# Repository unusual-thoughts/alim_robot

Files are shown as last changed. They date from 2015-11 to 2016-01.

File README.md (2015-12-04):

Réalisation de la carte d'alimentation
======================================

La carte d'alimentation est chargée de:
- Délivrer l'alimentation des différents composants du robot
- Informer de l'état de charge des batteries avec des leds
- Protéger les batteries

### Ancienne Carte

Un microcontrôleur Atmega328P utilisé pour évaluer la tension des batteries.

Les sources étaient trois batteries NiMh 12V de 2500mAh

Les régulateurs utilisés étaient DE-5W050 et DE-5WADJ

On peut utiliser des LM2596 a la place
Le plus simple serait de prendre des modules déja faits (très très peu chers)

### Budget Courant/tension

Elément            | U (V) | I (mA)             | P (W)
-------------------|-------|--------------------|------
Autres capteurs    | 3,3   | 5-50               | < .3
Raspberry          | 5     | 700 (1.5A max)     | < 7.5
Arduino/Teensy     | 5     | 10-20 (optimiste?) | ~.1
Capteurs           | 5     | 5-50               | < .5
Hokuyo             | 5     | 500 (800 init)     | < 4
Pont en H          | 5     | 5-10               | < .05
uArm               | 5     | < 5A               | < 25
Total 5V           | 5     | ~7A                | ~35
Servo Dynamixel    | 11.1  | 1.3A (x2)          | 28.86
Moteurs            | 24    | 800 (pic)          | < 38.4
Total (bat 1 et 2) | 24    | < 800              | < 38.4
Total (bat 3)      | 12    | < 5.42 A           | < 65

### Choix Régulateur(s)

Dynamixels non régulés? Ou step-down depuis le 24V? ou 12V?

Utilisation de [WEBENCH](http://webench.ti.com/) pour choix régulateur.

Régulateur                                            | Courant  | Package | Commentaires
------------------------------------------------------|----------|---------|----------------------------------------------
[Module LM2596](http://www.ebay.com/itm/321476590827) | << 3A    | Module  | Peu fiable (!)
[LM2596](http://www.ti.com/product/lm2596)            | max 3A   | ~TO263  | Pas assez de courant
[LM2678](http://www.ti.com/product/lm2678)            | max 5A   | ~TO263  | Fort encombrement, courant insuffisant, gros inducteur et diode
[TPS54821](http://www.ti.com/product/tps54821)        | max 8A   | QFN     | très performant, pas cher, très faible encombrement, compliqué à souder
[LMZ12008](http://www.ti.com/product/LMZ12008/)       | max 8A   | PFM     | très encombrant, très simple d'utilisation, extremement cher (15 euros)
[LMZ31710](http://www.ti.com/product/LMZ31710)        | max 10A  | QFN     | compromis, peu de composants externes, pas d'inducteur (!)

### Choix batterie 12V

On garde les 2 NiMh pour le 24V
LiPo pour le 12V:
[5800mAh](http://www.hobbyking.com/hobbyking/store/uh_viewItem.asp?idProduct=35957) ou [8000mAh](http://www.hobbyking.com/hobbyking/store/__38300__ZIPPY_Flightmax_8000mAh_3S1P_30C_Lipo_Pack_EU_Warehouse_.html)

### Schematic
#### Cicuit de protection batterie


#### Arduino


### Aperçu carte


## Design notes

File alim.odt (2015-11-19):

Réalisation de la carte d'alimentation

La carte d'alimentation est chargée :

-délivrer l'alimentation des différents composants du robot

-informer de l'état de charge des batteries avec des leds

Un microcontroleur Atmega328P sera utilisé pour évalué la tenion des batteries.

Les sources sont trois batteries 12V de 2500mAh

Les régulateurs utilisés sont DE-5W050 et DE-5WADJ

Entrés | Régulateur Dimension Engineering | Sortie
7-30V | | 5V 1A(max)

Elément | U (V) | I (mA) | Reg
Raspberry | 5 | 700
Arduino/Teensy | 5 | 10-20
Capteurs | 5 | 5-50
Autres capteurs | 3,3 | 5-50
Hokuyo | 5 | 500 (800 init)
Pont en H | 5 | 5-10
Servomoteurs (6) | 5-8 | 400 (800 max)
Autres actionneurs
Moteurs | 24 | ?

Démarche:

- Stratégie d'alimentation

- Représentation du schématics sous Eagle

- Agencement et réalisation de la carte

- Choix de la connectique

- Choix des régulateurs

- Choix du micro, ATTiny 48/85

-Choix de batterie 18-650

Tâche :

Programmer un Atmega328P

Utilisation d'Eagle (voir tutos de Jeremy Blum)

Matériel : Régulateur 5,1 V

Etat des lieux des régulateurs présent sur les cartes :

Teensy

Arduino

Raspberry

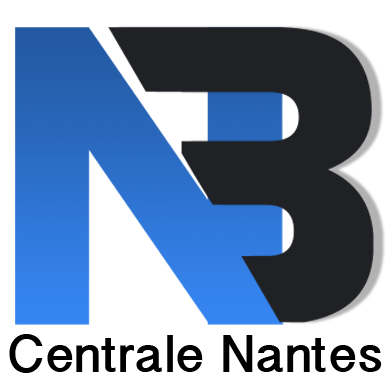
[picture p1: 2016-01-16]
eagle/artwork/Fanart.png

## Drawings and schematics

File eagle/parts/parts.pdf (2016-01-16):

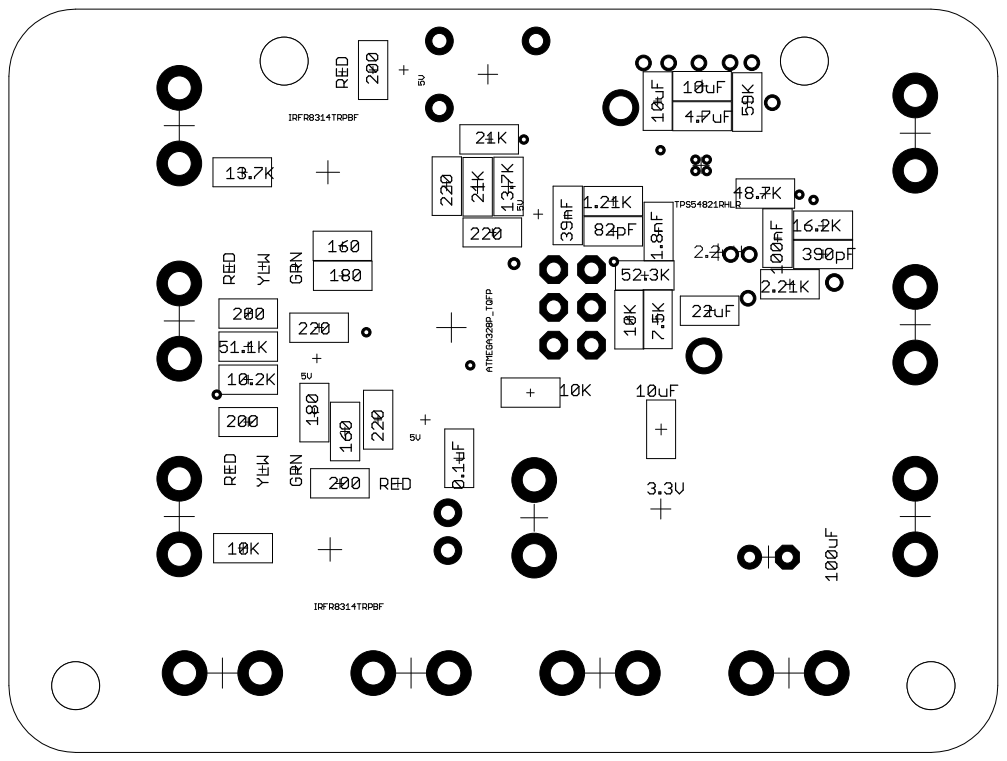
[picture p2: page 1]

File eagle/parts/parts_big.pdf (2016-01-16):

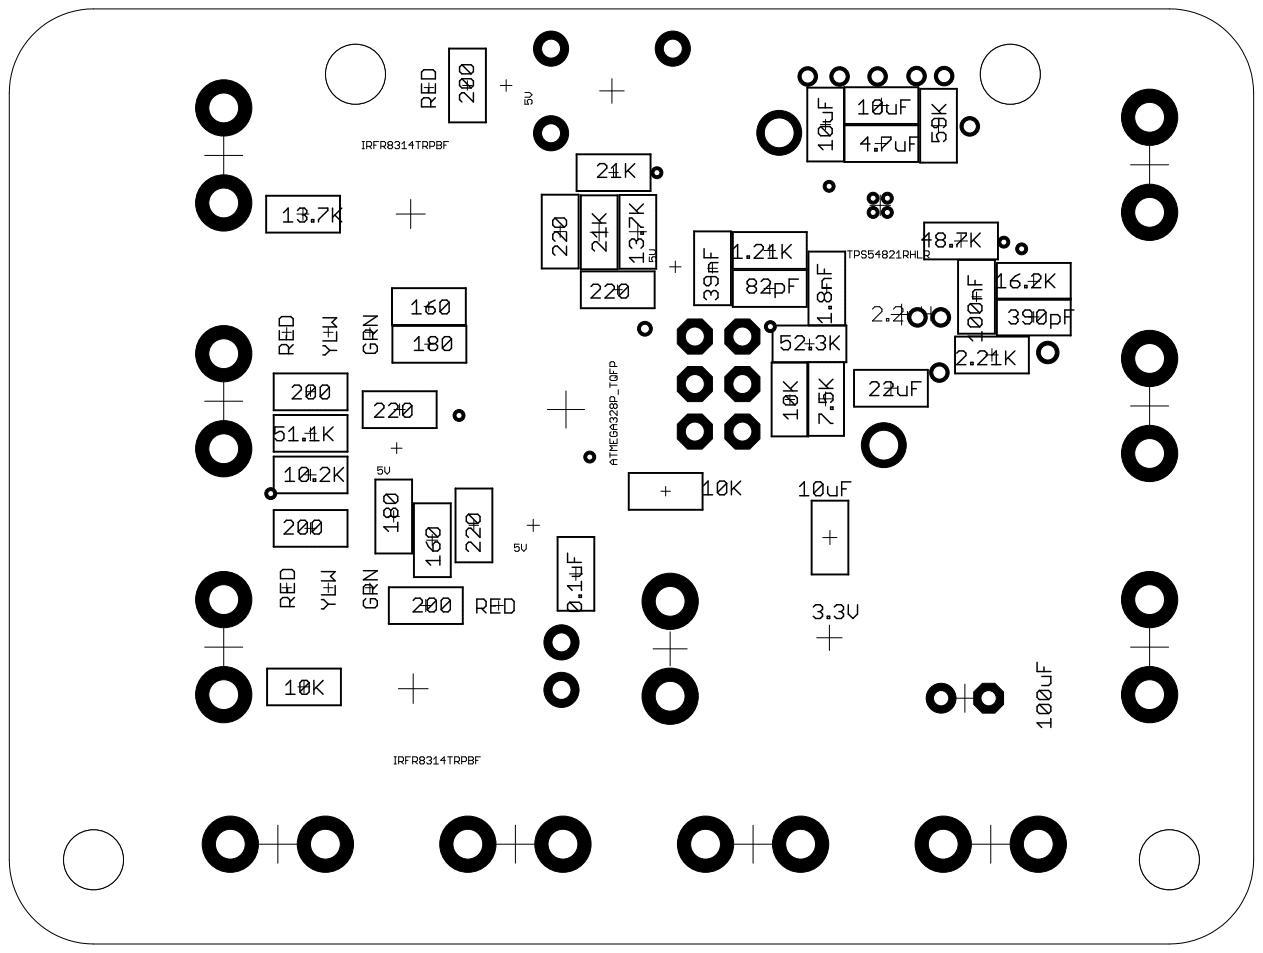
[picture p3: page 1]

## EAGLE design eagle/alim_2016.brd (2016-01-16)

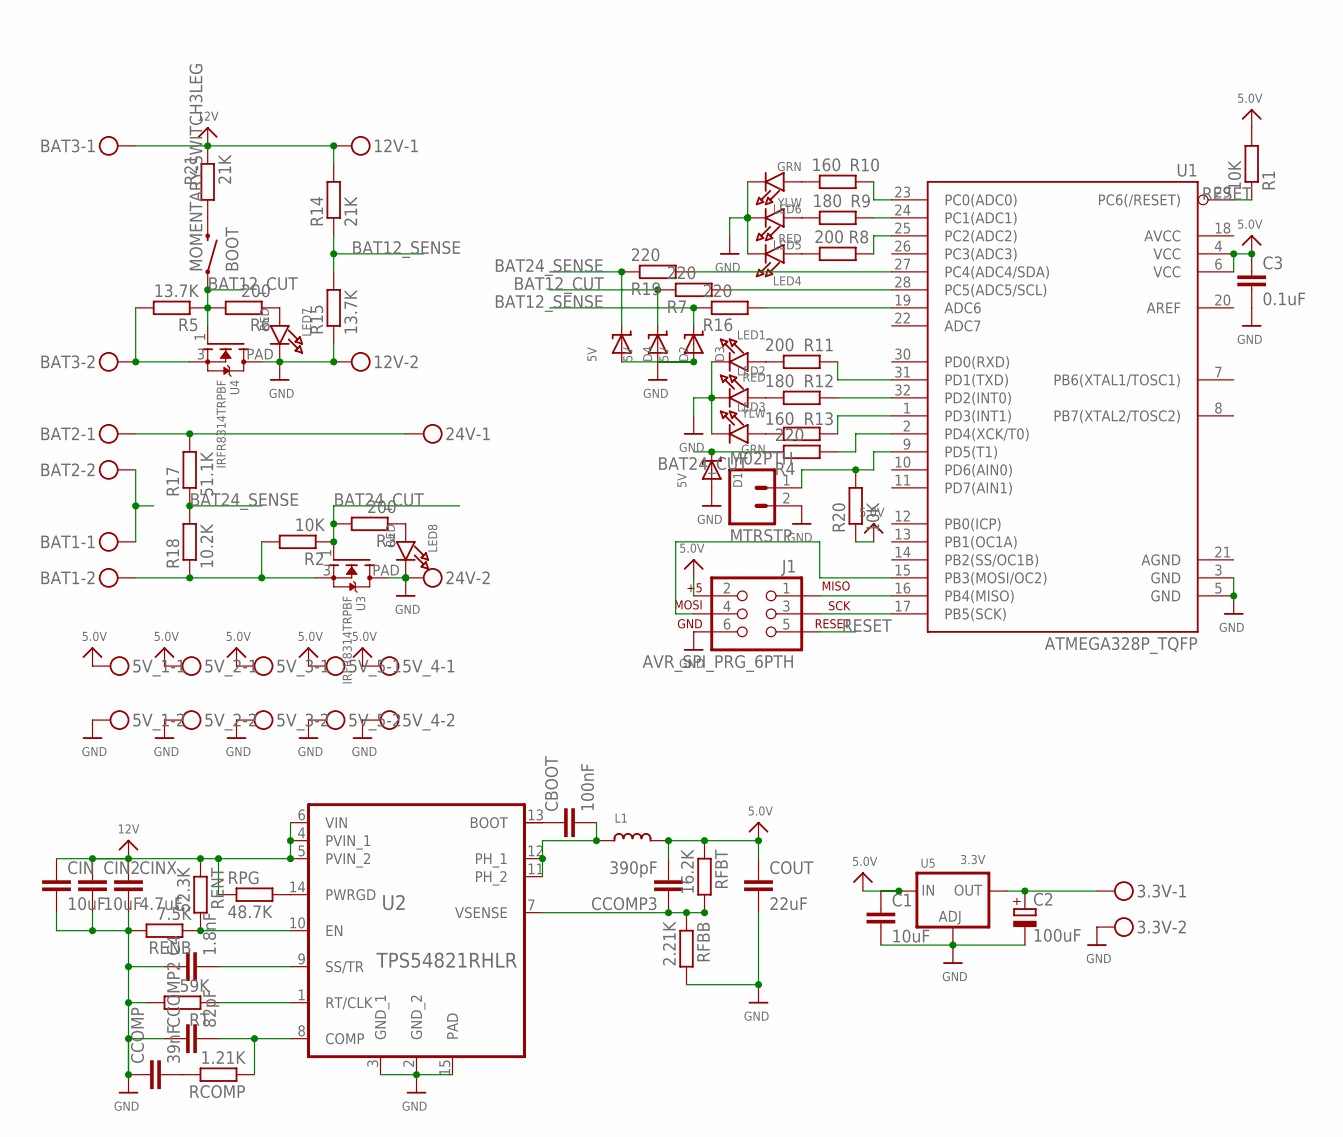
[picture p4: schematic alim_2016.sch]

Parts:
3.3V, 5V_1, 5V_2, 5V_3, 5V_4, 5V_5, 12V, 24V: WURTH_2PIN311; WURTH311
BAT1, BAT2, BAT3: WURTH_2PIN313; WURTH313_2
BOOT: MOMENTARY-SWITCH3LEG; 3LEGGED-TACT
C1: 10uF; C0805
C2: 100uF; E2,5-7
C3: 0.1uF; C0805
C4: 1.8nF; C0805
CBOOT: 100nF; C0805
CCOMP: 39nF; C0805
CCOMP2: 82pF; C0805
CCOMP3: 390pF; C0805
CIN, CIN2: 10uF; C0805
CINX: 4.7uF; C0805
COUT: 22uF; C0805
D1, D2, D3, D4: 5V; SOD-123
J1: AVR_SPI_PRG_6PTH; 2X3
L1: 2.2uH; XAL5030
LED1, LED4, LED7, LED8: RED; CHIPLED_0805_NOOUTLINE
LED2, LED5: YLW; CHIPLED_0805_NOOUTLINE
LED3, LED6: GRN; CHIPLED_0805_NOOUTLINE
MTRSTP: M02PTH; 1X02
R1, R2, R20: 10K; M0805
R3, R6, R8, R11: 200; M0805
R4, R7, R16, R19: 220; M0805
R5, R15: 13.7K; M0805
R9, R12: 180; M0805
R10, R13: 160; M0805
R14, R21: 21K; M0805
R17: 51.1K; M0805
R18: 10.2K; M0805
RCOMP: 1.21K; M0805
RENB: 7.5K; M0805
RENT: 52.3K; M0805
RFBB: 2.21K; M0805
RFBT: 16.2K; M0805
RPG: 48.7K; M0805
RT: 59K; M0805
U1: ATMEGA328P_TQFP; TQFP32-08
U2: TPS54821RHLR; S-PVQFN-N14
U3, U4: IRFR8314TRPBF; DPACK_1
U5: 3.3V; TO252

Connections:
5.0V: 5V_1.P$1, 5V_2.P$1, 5V_3.P$1, 5V_4.P$1, 5V_5.P$1, C1.1, C3.1, CCOMP3.2, COUT.1, J1.2, L1.2, R1.2, R20.1, RFBT.1, U1.4 (VCC), U1.6 (VCC), U5.2 (IN)
12V: 12V.P$1, BAT3.P$1, CIN.1, CIN2.1, CINX.1, R14.2, R21.1, RENT.1, RPG.1, U2.4 (PVIN_1), U2.5 (PVIN_2), U2.6 (VIN)
24V: 24V.P$1, BAT2.P$1, R17.2
BAT12_CUT: BOOT.1, D2.C, R5.1, R6.2, R7.1, U4.1 (G)
BAT12_SENSE: D3.C, R14.1, R15.2, R16.1
BAT24_CUT: D1.C, R2.1, R3.2, R4.1, U3.1 (G)
BAT24_SENSE: D4.C, R17.1, R18.2, R19.1
COMP: CCOMP2.2, RCOMP.1, U2.8 (COMP)
EN: RENB.1, RENT.2, U2.10 (EN)
GND: 3.3V.P$2, 5V_1.P$2, 5V_2.P$2, 5V_3.P$2, 5V_4.P$2, 5V_5.P$2, 12V.P$2, 24V.P$2, C1.2, C2.-, C3.2, C4.1, CCOMP.1, CCOMP2.1, CIN.2, CIN2.2, CINX.2, COUT.2, D1.A, D2.A, D3.A, D4.A, J1.6, LED1.C, LED2.C, LED3.C, LED4.C, LED5.C, LED6.C, LED7.C, LED8.C, MTRSTP.2, R15.1, RENB.2, RFBB.2, RT.2, U1.3 (GND), U1.5 (GND), U2.2 (GND_2), U2.3 (GND_1), U2.15 (PAD), U3.PAD (D), U4.PAD (D), U5.1 (ADJ)
MISO: J1.1, U1.16 (PB4(MISO))
MOSI: J1.4, U1.15 (PB3(MOSI/OC2))
unnamed: 3.3V.P$1, C2.+, U5.3 (OUT)
unnamed: R16.2, U1.19 (ADC6)
unnamed: BAT1.P$1, BAT2.P$2
unnamed: MTRSTP.1, R20.2, U1.9 (PD5(T1))
unnamed: BOOT.3 (2), R21.2
unnamed: BAT1.P$2, R2.2, R18.1, U3.3 (S)
unnamed: LED8.A, R3.1
unnamed: LED7.A, R6.1
unnamed: R4.2, U1.2 (PD4(XCK/T0))
unnamed: BAT3.P$2, R5.2, U4.3 (S)
unnamed: R9.2, U1.24 (PC1(ADC1))
unnamed: LED4.A, R8.1
unnamed: LED5.A, R9.1
unnamed: LED6.A, R10.1
unnamed: LED1.A, R11.1
unnamed: LED2.A, R12.1
unnamed: LED3.A, R13.1
unnamed: R8.2, U1.25 (PC2(ADC2))
unnamed: R10.2, U1.23 (PC0(ADC0))
unnamed: R7.2, U1.28 (PC5(ADC5/SCL))
unnamed: R13.2, U1.1 (PD3(INT1))
unnamed: R12.2, U1.32 (PD2(INT0))
unnamed: R11.2, U1.31 (PD1(TXD))
unnamed: R19.2, U1.27 (PC4(ADC4/SDA))
unnamed: CCOMP.2, RCOMP.2
unnamed: CBOOT.1, U2.13 (BOOT)
unnamed: RPG.2, U2.14 (PWRGD)
PH: CBOOT.2, L1.1, U2.11 (PH_2), U2.12 (PH_1)
RESET: J1.5, R1.1, U1.29 (PC6(/RESET))
RTCLK: RT.1, U2.1 (RT/CLK)
SCK: J1.3, U1.17 (PB5(SCK))
SSTR: C4.2, U2.9 (SS/TR)
VSENSE: CCOMP3.1, RFBB.1, RFBT.2, U2.7 (VSENSE)

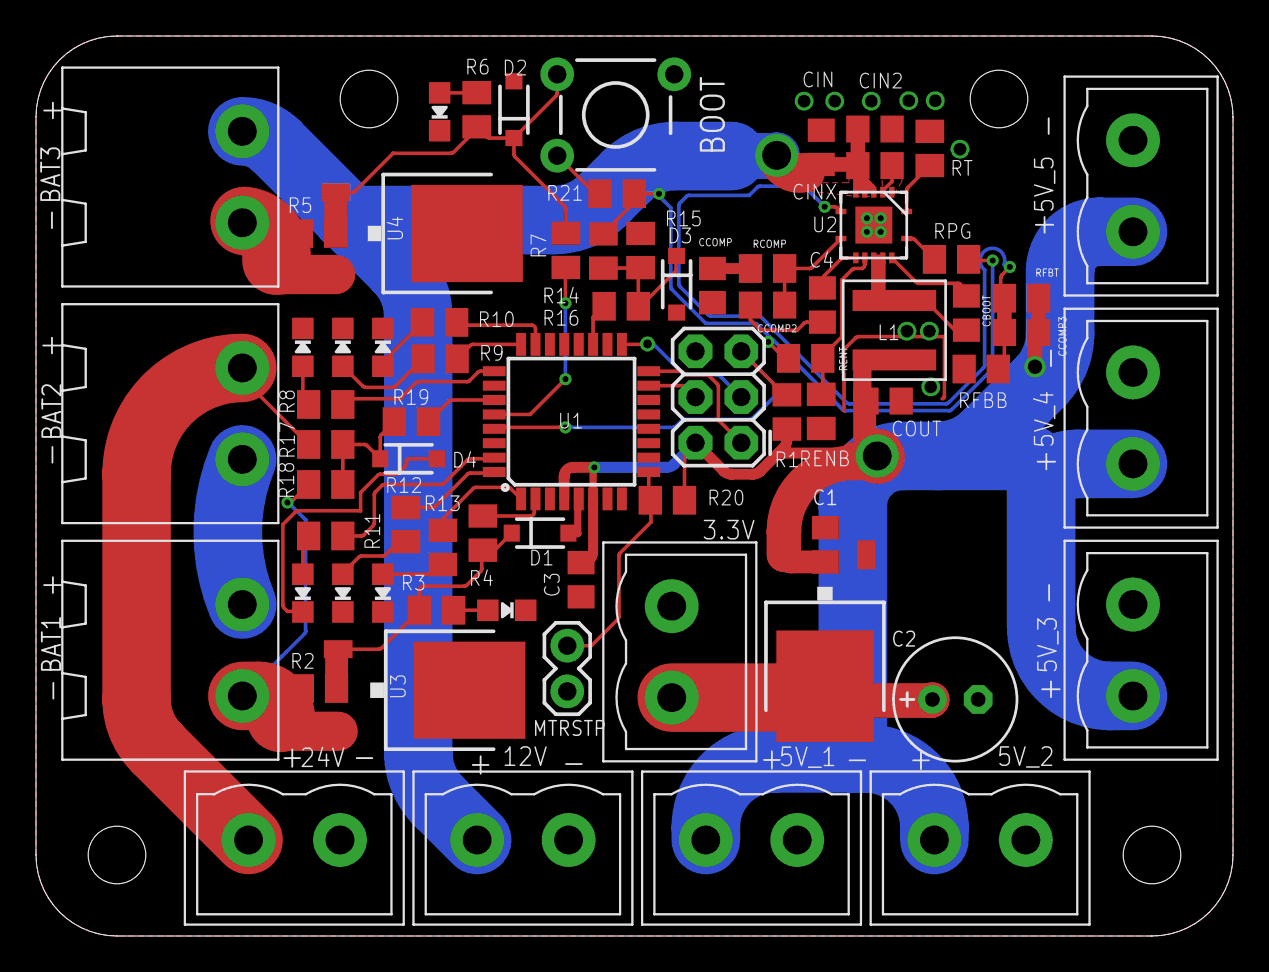
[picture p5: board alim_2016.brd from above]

Board: 2 copper layers, 66.5 x 50.0 mm, 72 parts (0 on the bottom side), 45 nets.

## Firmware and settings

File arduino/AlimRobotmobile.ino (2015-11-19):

/*Programme AlimRobotmobile
Ce programme permet de mesurer la tension des batteries et d'en déduire leur état de charge
*/


//Led RGB 1 elec
#define BLUE1 2
#define GREEN1 1
#define RED1 0

//Led RGB 2 power
#define BLUE2 5
#define GREEN2 4
#define RED2 3

#define powcheck 0 //24V puissance
#define eleccheck 3 //12V elec
#define powresistorfactor 0.18
#define elecresistorfactor 0.414

const int nelements=10;
const float ucharge=1.4;
const float unominale=1.25;
const float udecharge=1.1;
const float ucritique=0.9;
const float Ucharge=ucharge*nelements;//pour UNE batterie de 10 éléments soit environ 12V
const float Unominale=unominale*nelements;
const float Udecharge=udecharge*nelements;
const float Ucritique=ucritique*nelements;

void setup(){
  pinMode(BLUE1,OUTPUT);
  pinMode(GREEN1,OUTPUT);
  pinMode(RED1,OUTPUT);
  pinMode(BLUE2,OUTPUT);
  pinMode(GREEN2,OUTPUT);
  pinMode(RED2,OUTPUT);
  for(int i=0;i<10;i++){
    digitalWrite(BLUE1,1^(digitalRead(BLUE1)));
    digitalWrite(BLUE2,1^(digitalRead(BLUE2)));
    delay(100);
  }
}

void loop(){
  //----------------------
  float powval=float(analogRead(powcheck))*(5.0/1023)*(1/powresistorfactor);
  float elecval=float(analogRead(eleccheck))*(5.0/1023)*(1/elecresistorfactor);
  //-----------------------POWER-----------------------------------
  if(powval>2*Unominale){
    digitalWrite(RED2,LOW);
    digitalWrite(BLUE2,LOW);
    digitalWrite(GREEN2,HIGH);
  }else if((powval<2*Unominale)&&(powval>2*Udecharge)){
    digitalWrite(RED2,HIGH);
    digitalWrite(BLUE2,LOW);
    digitalWrite(GREEN2,HIGH);
  }else if((powval<2*Udecharge)&&(powval>2*Ucritique)){
    digitalWrite(RED2,HIGH);
    digitalWrite(BLUE2,LOW);
    digitalWrite(GREEN2,LOW);
  }else{
    digitalWrite(RED2,1^digitalRead(RED2));
    digitalWrite(BLUE2,LOW);
    digitalWrite(GREEN2,LOW);
  }
  //---------------------------ELEC----------------------------------
  if(elecval>Unominale){
    digitalWrite(RED1,LOW);
    digitalWrite(BLUE1,LOW);
    digitalWrite(GREEN1,HIGH);
  }else if((elecval<Unominale)&&(elecval>Udecharge)){
    digitalWrite(RED1,HIGH);
    digitalWrite(BLUE1,LOW);
    digitalWrite(GREEN1,HIGH);
  }else if((elecval<Udecharge)&&(elecval>Ucritique)){
    digitalWrite(RED1,HIGH);
    digitalWrite(BLUE1,LOW);
    digitalWrite(GREEN1,LOW);
  }else{
    digitalWrite(RED1,1^digitalRead(RED1));
    digitalWrite(BLUE1,LOW);
    digitalWrite(GREEN1,LOW);
  }
  delay(500);
}

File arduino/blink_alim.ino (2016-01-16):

#define LED_24_RED 1
#define LED_24_YLW 2
#define LED_24_GRN 3

#define LED_12_RED 16
#define LED_12_YLW 15
#define LED_12_GRN 14

void setup() {
  pinMode(1, OUTPUT);
}

void loop() {
  digitalWrite(LED_24_RED, HIGH);
  delay(100);
  digitalWrite(LED_24_RED, LOW);
  digitalWrite(LED_24_YLW, HIGH);
  delay(100);
  digitalWrite(LED_24_YLW, LOW);
  digitalWrite(LED_24_GRN, HIGH);
  delay(100);
  digitalWrite(LED_24_GRN, LOW);
  digitalWrite(LED_12_RED, HIGH);
  delay(100);
  digitalWrite(LED_12_RED, LOW);
  digitalWrite(LED_12_YLW, HIGH);
  delay(100);
  digitalWrite(LED_12_YLW, LOW);
  digitalWrite(LED_12_GRN, HIGH);
  delay(100);
  digitalWrite(LED_12_GRN, LOW);  
}

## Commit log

2015-11-19 add nicolas's files
    [alimrobotmobile.brd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]
2015-11-26 Update current budget
2015-11-28 add first draft for new board
    [alim_2016.brd, alim_2016.sch]
2015-11-28 thermal vias
    [alim_2016.brd, alim_2016.sch]
2015-11-29 pcb rearranging
    [alim_2016.brd, alim_2016.sch]
2015-11-29 remove extra switch, routing
    [alim_2016.brd, alim_2016.sch]
2015-11-29 adding battery voltage sense
    [alim_2016.brd, alim_2016.sch]
2015-11-29 adding other battery voltage sense
    [alim_2016.brd, alim_2016.sch]
2015-11-29 clean up schematic
    [alim_2016.sch]
2015-11-30 clean up board
    [alim_2016.brd, alim_2016.sch]
2015-12-01 most of the circuit finished
    [alim_2016.brd, alim_2016.sch]
2015-12-01 more cleanup
    [alim_2016.brd, alim_2016.sch]
2015-12-01 rearrange stuff
    [alim_2016.brd, alim_2016.sch]
2015-12-01 Update current draw
2015-12-03 add new switching regulator
    [alim_2016.brd, alim_2016.sch]
2015-12-03 add schematic preview
2015-12-04 add board preview
2015-12-07 route TPS chip
    [alim_2016.brd, alim_2016.sch]
2015-12-23 changed connectors
    [alim_2016.brd, alim_2016.sch]
2015-12-23 shuffle things around
    [alim_2016.brd]
2015-12-30 final version
    [alim_2016.brd, alim_2016.sch]
2016-01-09 board sent to OSHPARK
    [alim_2016.brd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]
2016-01-16 fix routing error: ADC7 cannot be a GPIO
    [alim_2016.brd, alim_2016.sch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]
2016-01-16 added arduino board config and test sketch
2016-01-16 increase via tenting
    [alim_2016.brd]

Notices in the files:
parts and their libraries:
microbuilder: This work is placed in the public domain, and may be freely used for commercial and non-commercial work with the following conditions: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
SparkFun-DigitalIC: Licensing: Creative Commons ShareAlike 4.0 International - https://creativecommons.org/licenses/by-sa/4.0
